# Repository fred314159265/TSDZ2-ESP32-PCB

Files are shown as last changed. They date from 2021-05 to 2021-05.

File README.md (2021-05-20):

# Alternative TSDZ2-ESP32 Bluetooth PCB

⚠⚠⚠ This is current untested - not fit for use *yet*! ⚠⚠⚠

This repository is an updated version of MSpider65's [TSDZ2-ESP32-PCB](https://github.com/TSDZ2-ESP32/TSDZ2-ESP32-PCB) project. If you are not familiar with the original project, it is a PCB and some custom firmware (plus Android app) that make the TSDZ2 eBike mid-drive kit smarter (fully customisable settings, log power, speed, etc.) and higher performance. It's a really fantastic project and definitely worth checking out if you're considering the TSDZ2 eBike mid-drive kit.

For more information on the project, see Mspider65's wiki page: [wiki.](https://github.com/TSDZ-ESP32/TSDZ-ESP32-wiki/wiki)

This update aims to make it more affordable (~$12 vs ~$23 for components). It also aims to use components that are generally slightly easier to solder by hand. It has been done in [KiCAD](https://www.kicad.org), ensuring full control of the source design files.

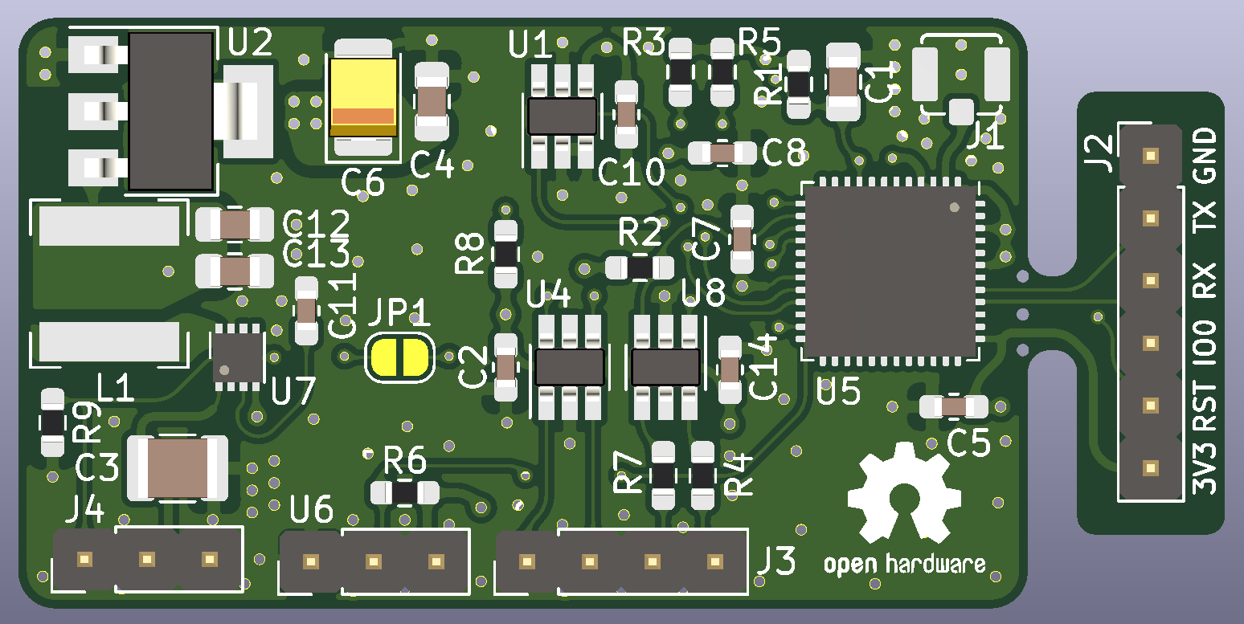
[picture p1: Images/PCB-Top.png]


## Changes

- All connector are now 0.1" pin headers. The intention for these (except the programming connector) is to directly solder the TSDZ2's wires to these as pads instead of actually using pin headers. Being 0.1", some connectors (JST XH?) will also fit, and you are welcome to use as desired.

- 5V and 3.3V regulator changes - cost savings.

- Programming header now uses RST and GPIO0 pins directly (no need for jumpers), with the intention of using RTS and CTS lines of a USB-to-serial adaptor to automate putting the ESP32 in bootloader mode. More information can be found [here](https://github.com/espressif/esptool/wiki/ESP32-Boot-Mode-Selection#automatic-bootloader).
  
  TLDR: connect RST and GPIO0 pins to USB-to-serial adaptor like so, and programming should "just work". 
  
  ⚠ **Make sure you only power the board via 3.3V!** ⚠
  
  | Programming Header Pin | USB-to-serial Pin |
  | ---------------------- | ----------------- |
  | RST                    | RTS               |
  | IO0                    | DTR               |
  
- Temperature sensor changed to much cheaper and also lower spec device. (Cause for firmware update.) Still is plenty accurate enough for monitoring PCB temperature and is much cheaper.

- Added solder bridge pads - removes need for diode. Make sure you bridge these with a soldering iron after programming the ESP32.

- Programming header is on breakoff part of board.

- Redrawn from scratch in KiCAD.

## Pinout

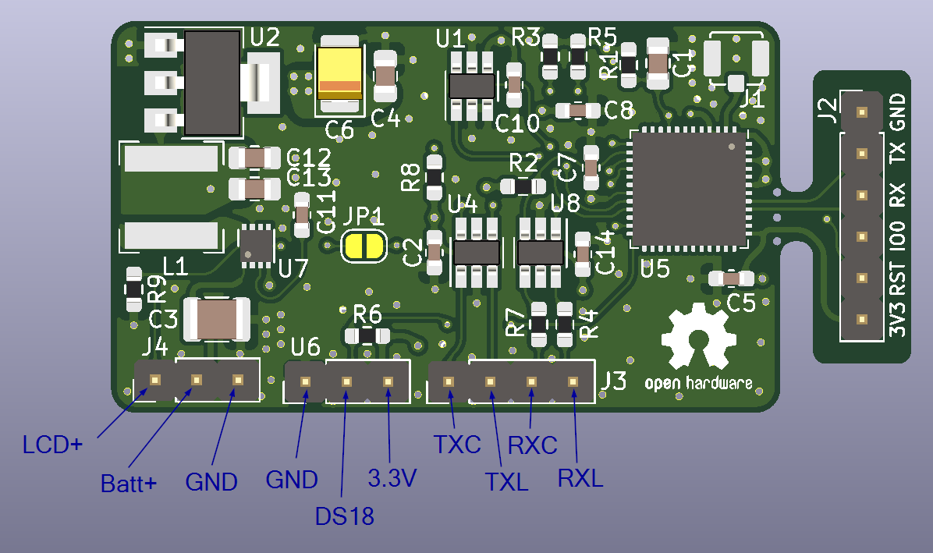
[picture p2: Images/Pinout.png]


## FAQs

#### Why not use MSpider65's original PCB design?

I have use the original design and it works very well. After needing another PCB recently I saw that many of the components have become very expensive (general silicon shortage at this time...). This updated board aims to be much cheaper while having the same functionality and remaining the same size. This will require an update to the ESP32's firmware, but this should be a small change.

#### What's with the bit of the PCB sticking out?

This is for programming the ESP32 with a USB-to-serial adaptor. Once the ESP32 has been programmed, cut the tracks on the top and the bottom with a knife and then snap it off. MSpider65's project allows OTA (over-the-air) firmware updates so you won't be needing it again.

#### I successfully programmed the ESP32 but the board won't turn on when connected to battery power?

After programming, you need to short JP1 & JP2 on the PCB with a soldering iron. This is instead of using a diode in the design. (Slight cost saving and more efficient.) A trade-off I personally like in this case. Let me know if you prefer a diode...

#### Why is there a USB-to-Serial adaptor in the BOM?

As part of the aim to keep cost to a minimum, all items can be sourced from [LCSC](https://lcsc.com). Both the USB-to-serial adaptors and 2.4GHz antenna are quite inexpensive from LCSC and so have been included in the BOM for convenience. Of course if you are making more than one board you only require one USB-to-serial adaptor, but multiple antennas.

#### How can I order the PCB?

You can order the bare PCB from [JLCPCB](https://jlcpcb.com). You will need to select 4-layers, 0.8mm thickness and "JLC7629" controlled impedance. I also recommend getting a stencil and using solder paste. 

Example of suitable PCB options:

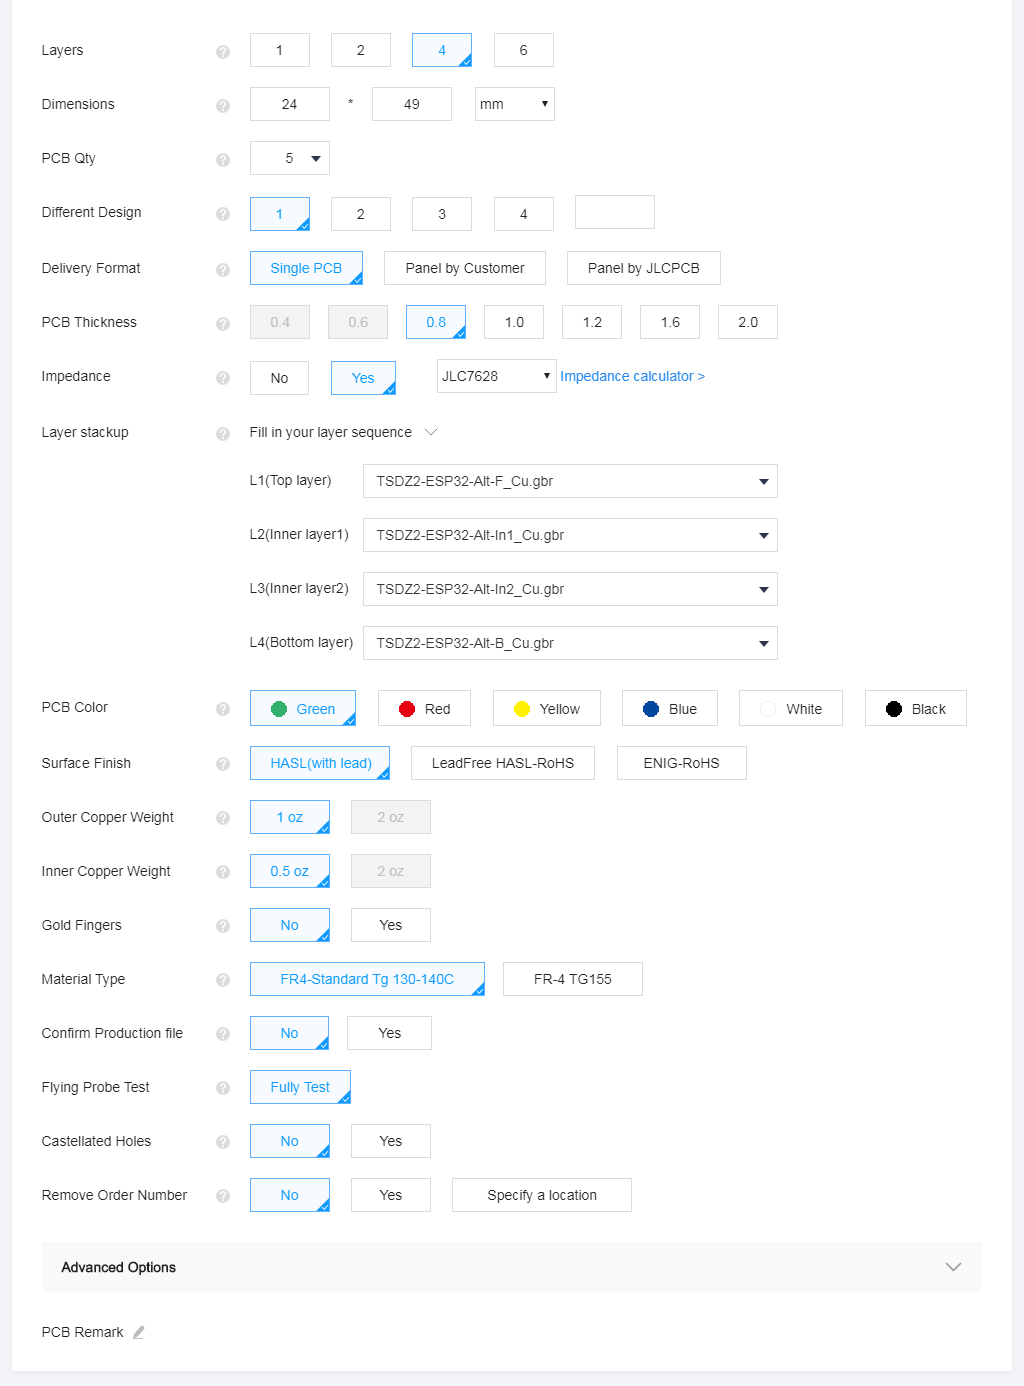
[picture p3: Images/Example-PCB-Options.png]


#### How can I order the components?

Upload "TSDZ2-ESP32-Alt_BOM.csv" to the "BOM tool" on LCSC [here](https://lcsc.com/bom.html#/upload). Only select quantity and part number columns. Be sure to adjust how many USB-to-serial adaptors you require before checking out. Also note that currently if you order the PCB before the components (from JLCPCB) you can get a discount on postage with LCSC at checkout.

#### How did you curve tracks/add teardrops?

By using the [KiCAD round tracks](https://github.com/mitxela/kicad-round-tracks) and [teardrops](https://github.com/NilujePerchut/kicad_scripts/tree/master/teardrops) plugins.

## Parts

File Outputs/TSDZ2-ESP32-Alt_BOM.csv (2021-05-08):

Item | Qty | Reference(s) | Value | LibPart | Footprint | Datasheet | LCSC Part # | Voltage
1 | 1 | AE1 | 2.4GHz Antenna | Device:Antenna |  | https://datasheet.lcsc.com/lcsc/1912111437_HI-LINK-HLK-TX-PCB-B_C209923.pdf | C209923
2 | 4 | C1, C4, C12, C13 | 4.7uF | Device:C | Capacitor_SMD:C_0805_2012Metric_Pad1.15x1.40mm_HandSolder | ~ | C98195
3 | 6 | C2, C5, C7, C8, C10, C14 | 100nF | Device:C | Capacitor_SMD:C_0603_1608Metric_Pad1.05x0.95mm_HandSolder | ~ | C14663
4 | 1 | C3 | 4.7uF | Device:C | Capacitor_SMD:C_1210_3225Metric | https://datasheet.lcsc.com/lcsc/2007091536_Taiyo-Yuden-HMK325C7475KN-TE_C697607.pdf | C697607 | 100V
5 | 1 | C6 | 47uF | Device:CP1 | Capacitor_Tantalum_SMD:CP_EIA-3528-21_Kemet-B_Pad1.50x2.35mm_HandSolder | ~ | C116617
6 | 1 | C11 | 1uF | Device:C | Capacitor_SMD:C_0603_1608Metric_Pad1.05x0.95mm_HandSolder | ~ | C59782
7 | 1 | J1 | ANT | Connector:Conn_Coaxial | TSDZ2-ESP32-Alt:U.FL-R-SMT-1(80) | https://datasheet.lcsc.com/lcsc/1811091710_HRS-Hirose-U-FL-R-SMT-1-80_C88374.pdf | C88374
8 | 1 | J2 | PROG_UART | Connector_Generic:Conn_01x06 | Connector_PinHeader_2.54mm:PinHeader_1x06_P2.54mm_Vertical | ~
9 | 1 | J3 | Conn_01x04 | Connector_Generic:Conn_01x04 | Connector_PinHeader_2.54mm:PinHeader_1x04_P2.54mm_Vertical | ~ | -
10 | 1 | J4 | Power | Connector_Generic:Conn_01x03 | Connector_PinHeader_2.54mm:PinHeader_1x03_P2.54mm_Vertical | ~ | -
11 | 1 | JP1 | JMP | Device:Jumper_NO_Small | Jumper:SolderJumper-2_P1.3mm_Open_RoundedPad1.0x1.5mm | ~ | -
12 | 1 | JP2 | JMP_3V3 | Device:Jumper_NO_Small | Jumper:SolderJumper-2_P1.3mm_Open_RoundedPad1.0x1.5mm | ~ | -
13 | 1 | L1 | 47uH | Device:L_Core_Ferrite_Small | Inductor_SMD:L_Bourns-SRN6028 | https://datasheet.lcsc.com/lcsc/2003172236_YJYCOIN-YNR6028-470M_C497831.pdf | C497831
14 | 5 | R1, R2, R3, R5, R8 | 10k | Device:R | Resistor_SMD:R_0603_1608Metric_Pad0.98x0.95mm_HandSolder | ~ | C25804
15 | 2 | R4, R7 | 330R | Device:R | Resistor_SMD:R_0603_1608Metric_Pad0.98x0.95mm_HandSolder | ~ | C23138
16 | 1 | R6 | 4.7k | Device:R | Resistor_SMD:R_0603_1608Metric_Pad0.98x0.95mm_HandSolder | ~ | C25999
17 | 1 | R9 | 1M | Device:R | Resistor_SMD:R_0603_1608Metric_Pad0.98x0.95mm_HandSolder | ~ | C26098
18 | 1 | U1 | TMP100 | Sensor_Temperature:TMP100 | Package_TO_SOT_SMD:SOT-23-6_Handsoldering | http://www.ti.com/lit/gpn/tmp100 | C31810
19 | 1 | U2 | AMS1117-3.3 | Regulator_Linear:AMS1117-3.3 | Package_TO_SOT_SMD:SOT-223-3_TabPin2 | http://www.advanced-monolithic.com/pdf/ds1117.pdf | C6186
20 | 1 | U3 | Ai-Thinker-CP2102 | TSDZ2-ESP32-Alt:Ai-Thinker-CP2102 |  | https://datasheet.lcsc.com/lcsc/Ai-Thinker-CP2102_C192392.pdf | C192392
21 | 2 | U4, U8 | SN74LVC2G17DBVR | TSDZ2-ESP32-Alt:SN74LVC2G17DBVR | Package_TO_SOT_SMD:SOT-23-6_Handsoldering | https://datasheet.lcsc.com/lcsc/Texas-Instruments-TI-SN74LVC2G17DBVR_C10429.pdf | C10429
22 | 1 | U5 | ESP32-PICO-D4 | RF_Module:ESP32-PICO-D4 | Package_DFN_QFN:QFN-48-1EP_7x7mm_P0.5mm_EP5.3x5.3mm | https://www.espressif.com/sites/default/files/documentation/esp32-pico-d4_datasheet_en.pdf | C193707
23 | 1 | U6 | DS18B20 | Sensor_Temperature:DS18B20 | Connector_PinHeader_2.54mm:PinHeader_1x03_P2.54mm_Vertical | http://datasheets.maximintegrated.com/en/ds/DS18B20.pdf | C376006
24 | 1 | U7 | MAX15062BATA+T | Regulator_Switching:MAX15062B | Package_DFN_QFN:DFN-8_2x2mm_P0.5mm | http://datasheets.maximintegrated.com/en/ds/MAX15062.pdf | C143362

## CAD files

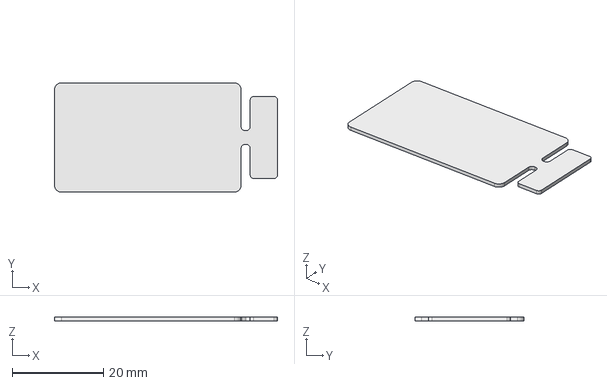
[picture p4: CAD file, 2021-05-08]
MCAD/PCB_Outline.FCStd
49.0 x 24.0 x 0.8 mm

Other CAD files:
MCAD/PCB_Outline.dxf

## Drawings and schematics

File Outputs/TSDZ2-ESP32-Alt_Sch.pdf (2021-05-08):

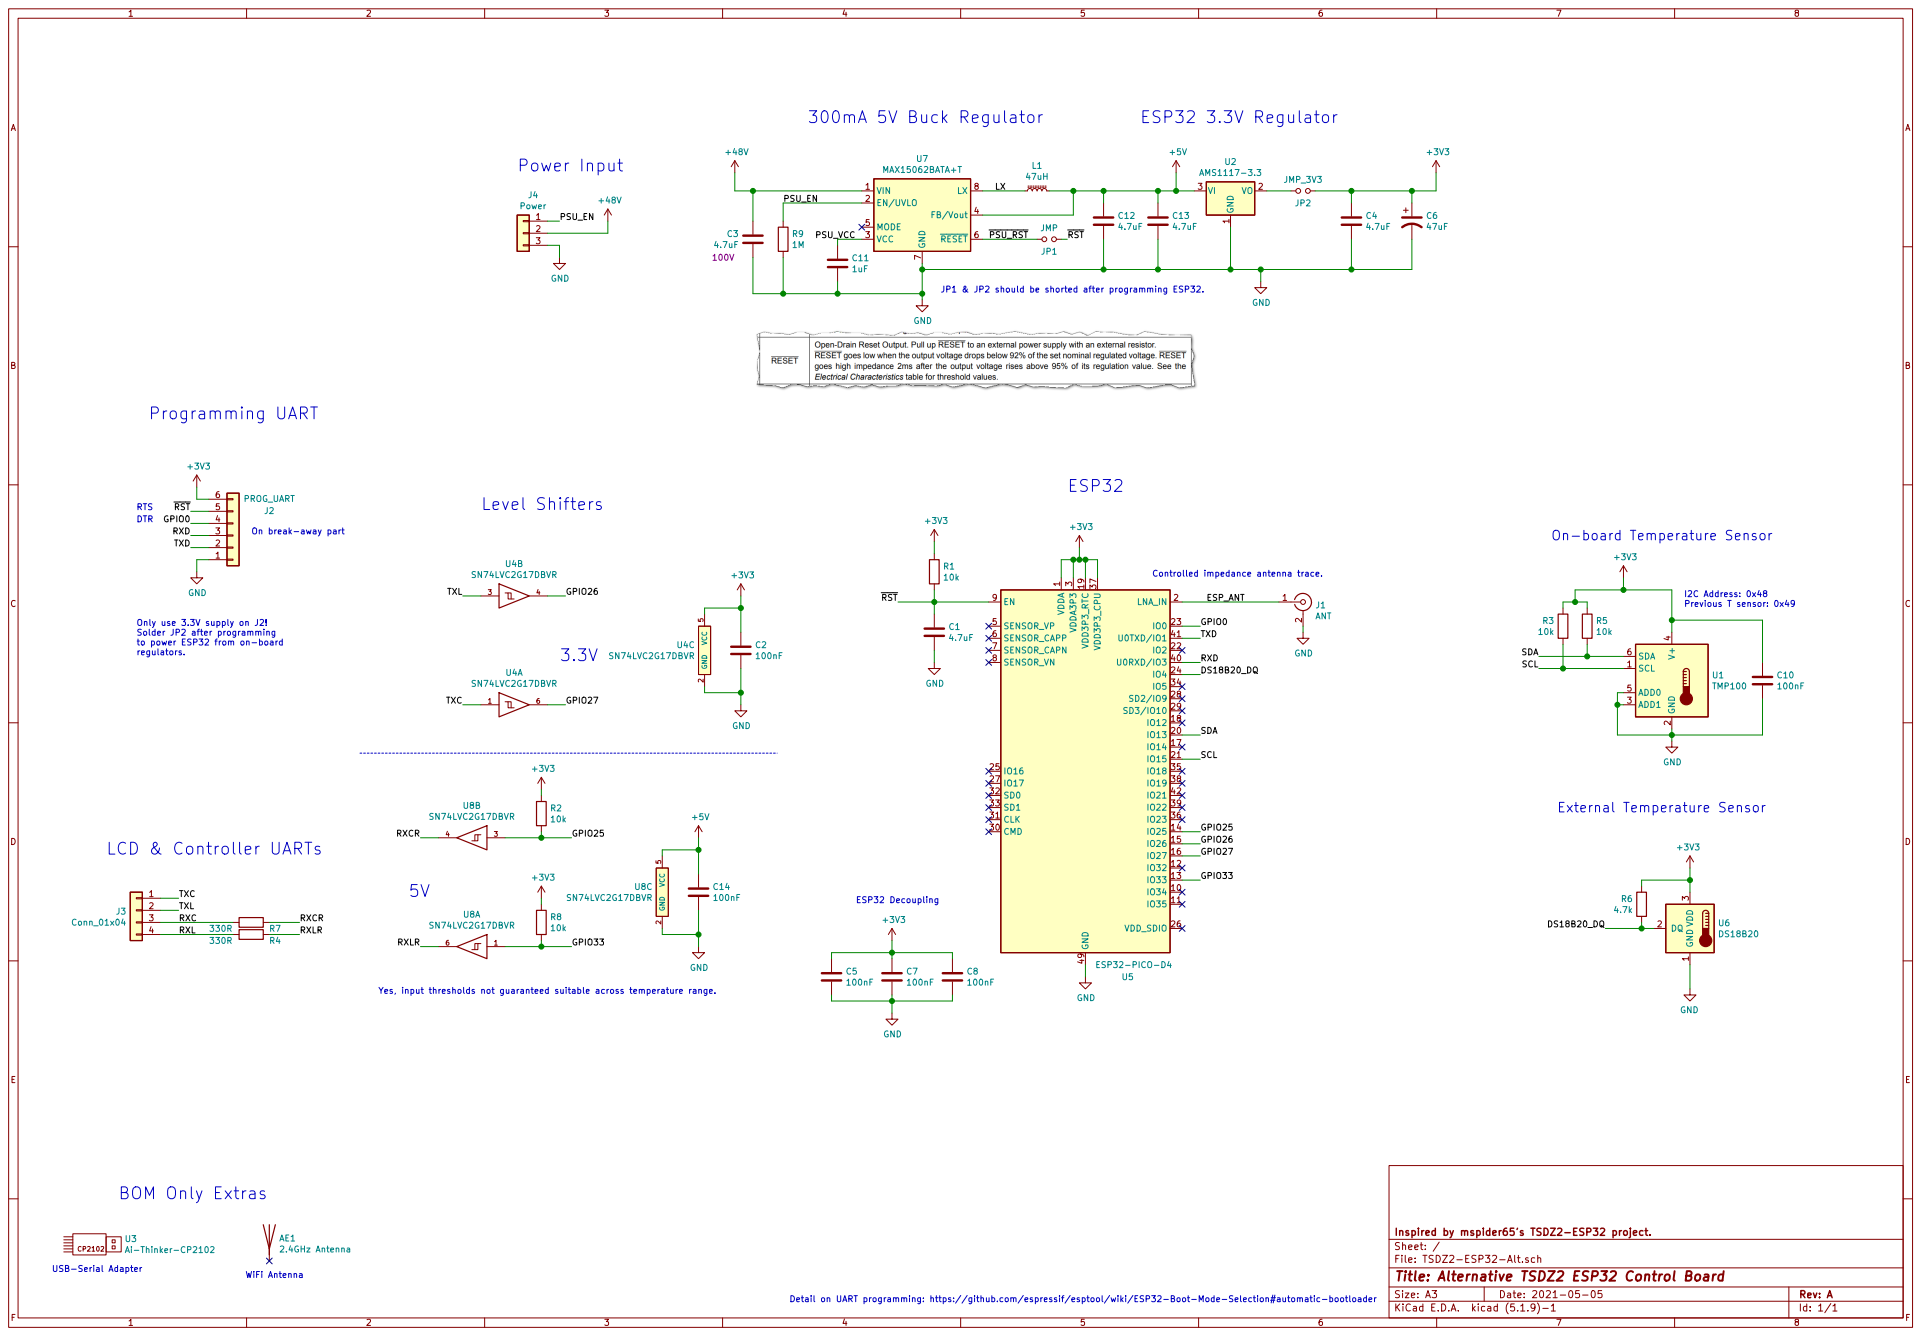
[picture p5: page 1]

I2C Address: 0x48 Previous T sensor: 0x49 ESP32 3.3V Regulator

PSU_EN GPIO0 RST Only use 3.3V supply on J2!

JP1 & JP2 should be shorted after programming ESP32.

On break-away part

On-board Temperature Sensor

Controlled impedance antenna trace.

Solder JP2 after programming
to power ESP32 from on-board

Yes, input thresholds not guaranteed suitable across temperature range.

Inspired by mspider65's TSDZ2-ESP32 project.
File: TSDZ2-ESP32-Alt.sch Sheet: /
Id: 1/1 Title: Alternative TSDZ2 ESP32 Control Board

WiFi Antenna USB-Serial Adapter

Detail on UART programming: https://github.com/espressif/esptool/wiki/ESP32-Boot-Mode-Selection#automatic-bootloader

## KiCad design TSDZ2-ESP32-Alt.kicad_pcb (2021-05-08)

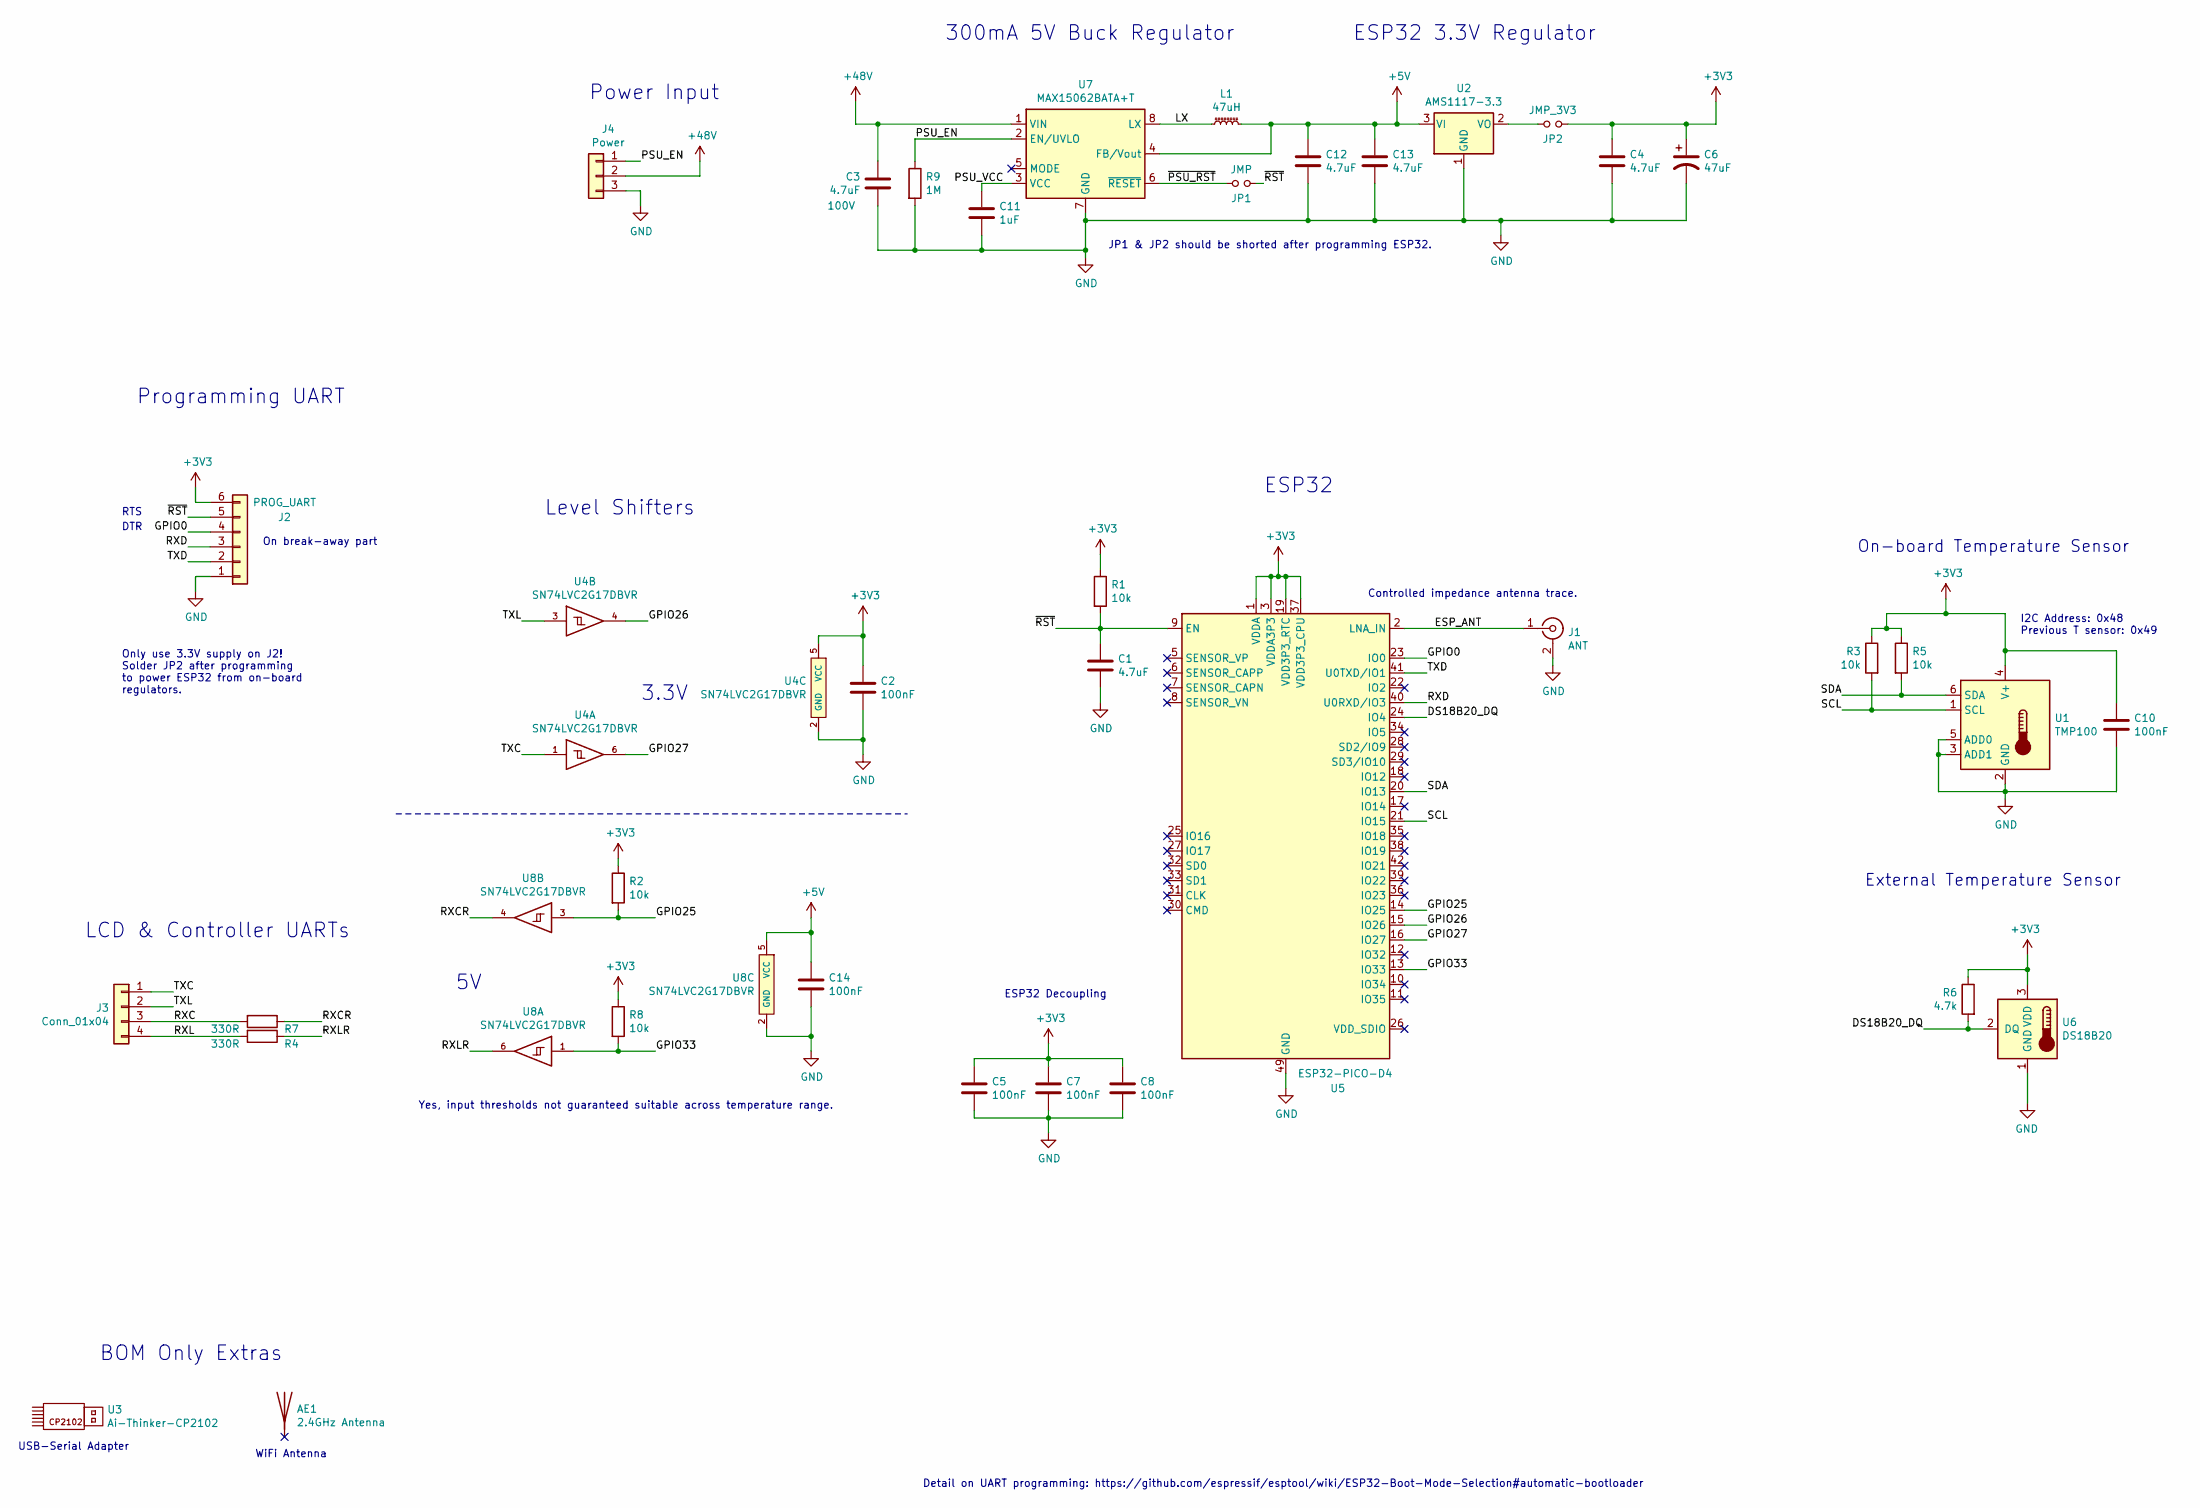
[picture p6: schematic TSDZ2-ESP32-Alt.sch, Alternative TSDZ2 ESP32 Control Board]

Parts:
AE1: 2.4GHz Antenna; LCSC Part # C209923
C1, C4, C12, C13: 4.7uF; C_0805_2012Metric_Pad1.15x1.40mm_HandSolder; LCSC Part # C98195
C2, C5, C7, C8, C10, C14: 100nF; C_0603_1608Metric_Pad1.05x0.95mm_HandSolder; LCSC Part # C14663
C3: 4.7uF; C_1210_3225Metric; Voltage 100V; LCSC Part # C697607
C6: 47uF; CP_EIA-3528-21_Kemet-B_Pad1.50x2.35mm_HandSolder; LCSC Part # C116617
C11: 1uF; C_0603_1608Metric_Pad1.05x0.95mm_HandSolder; LCSC Part # C59782
J1: ANT; U.FL-R-SMT-1(80); LCSC Part # C88374
J2: PROG_UART; PinHeader_1x06_P2.54mm_Vertical
J3: Conn_01x04; PinHeader_1x04_P2.54mm_Vertical
J4: Power; PinHeader_1x03_P2.54mm_Vertical
JP1: JMP; SolderJumper-2_P1.3mm_Open_RoundedPad1.0x1.5mm
JP2: JMP_3V3; SolderJumper-2_P1.3mm_Open_RoundedPad1.0x1.5mm
L1: 47uH; L_Bourns-SRN6028; LCSC Part # C497831
R1, R2, R3, R5, R8: 10k; R_0603_1608Metric_Pad0.98x0.95mm_HandSolder; LCSC Part # C25804
R4, R7: 330R; R_0603_1608Metric_Pad0.98x0.95mm_HandSolder; LCSC Part # C23138
R6: 4.7k; R_0603_1608Metric_Pad0.98x0.95mm_HandSolder; LCSC Part # C25999
R9: 1M; R_0603_1608Metric_Pad0.98x0.95mm_HandSolder; LCSC Part # C26098
U1: TMP100; SOT-23-6_Handsoldering; LCSC Part # C31810
U2: AMS1117-3.3; SOT-223-3_TabPin2; LCSC Part # C6186
U3: Ai-Thinker-CP2102; LCSC Part # C192392
U4, U8: SN74LVC2G17DBVR; SOT-23-6_Handsoldering; LCSC Part # C10429
U5: ESP32-PICO-D4; QFN-48-1EP_7x7mm_P0.5mm_EP5.3x5.3mm; LCSC Part # C193707
U6: DS18B20; PinHeader_1x03_P2.54mm_Vertical; LCSC Part # C376006
U7: MAX15062BATA+T; DFN-8_2x2mm_P0.5mm; LCSC Part # C143362

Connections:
+3V3: C2.1, C4.1, C5.1, C6.1, C7.1, C8.1, C10.1, J2.6, JP2.2, R1.1, R2.1, R3.1, R5.1, R6.1, R8.1, U1.4 (V+), U4.5 (VCC), U5.1 (VDDA), U5.3 (VDDA3P3), U5.4 (VDDA3P3), U5.19 (VDD3P3_RTC), U5.37 (VDD3P3_CPU), U5.43 (VDDA), U5.46 (VDDA), U6.3 (VDD)
+5V: C12.1, C13.1, C14.1, L1.2, U2.3 (VI), U7.4 (FB/Vout), U8.5 (VCC)
+48V: C3.1, J4.2, U7.1 (VIN)
/DS18B20_DQ: R6.2, U5.24 (IO4), U6.2 (DQ)
/ESP_ANT: J1.1 (In), U5.2 (LNA_IN)
/GPIO0: J2.4, U5.23 (IO0)
/GPIO25: R2.2, U5.14 (IO25), U8.3
/GPIO26: U4.4, U5.15 (IO26)
/GPIO27: U4.6, U5.16 (IO27)
/GPIO33: R8.2, U5.13 (IO33), U8.1
/LX: L1.1, U7.8 (LX)
/PSU_EN: J4.1, R9.1, U7.2 (EN/UVLO)
/PSU_VCC: C11.1, U7.3 (VCC)
/RXC: J3.3, R7.2
/RXCR: R7.1, U8.4
/RXD: J2.3, U5.40 (U0RXD/IO3)
/RXL: J3.4, R4.2
/RXLR: R4.1, U8.6
/SCL: R3.2, U1.1 (SCL), U5.21 (IO15)
/SDA: R5.2, U1.6 (SDA), U5.20 (IO13)
/TXC: J3.1, U4.1
/TXD: J2.2, U5.41 (U0TXD/IO1)
/TXL: J3.2, U4.3
/~PSU_RST: JP1.1, U7.6 (~RESET)
/~RST: C1.1, J2.5, JP1.2, R1.2, U5.9 (EN)
GND: C1.2, C2.2, C3.2, C4.2, C5.2, C6.2, C7.2, C8.2, C10.2, C11.2, C12.2, C13.2, C14.2, J1.2 (Ext), J2.1, J4.3, R9.2, U1.2 (GND), U1.3 (ADD1), U1.5 (ADD0), U2.1 (GND), U4.2 (GND), U5.49 (GND), U6.1 (GND), U7.7 (GND), U8.2 (GND)
unnamed: JP2.1, U2.2 (VO)

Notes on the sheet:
Controlled impedance antenna trace.
Level Shifters
BOM Only Extras
ESP32 Decoupling
External Temperature Sensor
On-board Temperature Sensor
I2C Address: 0x48 Previous T sensor: 0x49
ESP32 3.3V Regulator
300mA 5V Buck Regulator
Power Input
WiFi Antenna
USB-Serial Adapter
ESP32
3.3V
LCD & Controller UARTs
Detail on UART programming: https://github.com/espressif/esptool/wiki/ESP32-Boot-Mode-Selection#automatic-bootloader
Programming UART
JP1 & JP2 should be shorted after programming ESP32.
DTR
RTS
On break-away part
Only use 3.3V supply on J2! Solder JP2 after programming to power ESP32 from on-board regulators.
Yes, input thresholds not guaranteed suitable across temperature range.

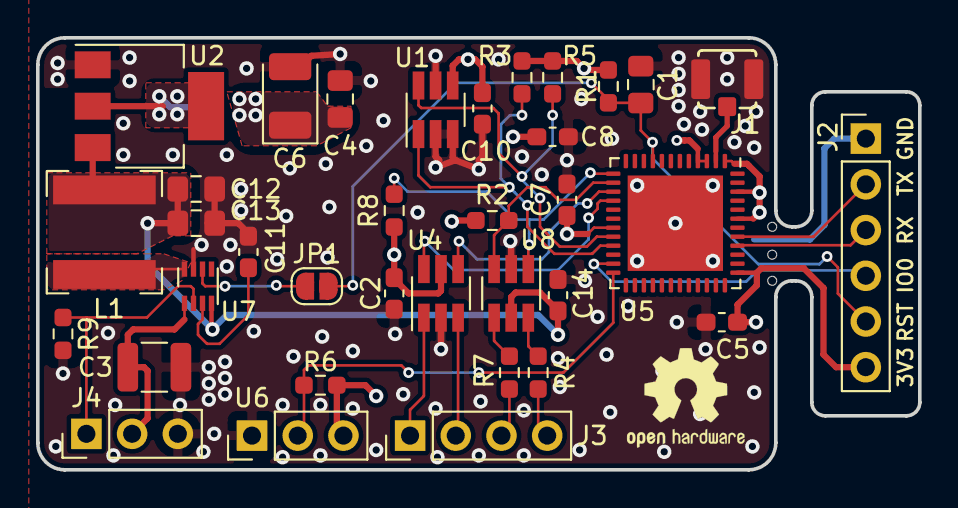
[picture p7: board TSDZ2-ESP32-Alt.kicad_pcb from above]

Board: 4 copper layers, 49.0 x 24.0 mm, 36 parts (1 on the bottom side), 27 nets.

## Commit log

2021-05-08 Initial alternative version of PCB release.
    [BOM_TSDZ2-ESP32.xlsx, ESP32.sch, PCB_Outline.FCStd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]
2021-05-22 Added interactive BOM file.
